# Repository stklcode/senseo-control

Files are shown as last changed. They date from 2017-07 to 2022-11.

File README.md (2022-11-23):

View this project on [CADLAB.io](https://cadlab.io/node/863). 

# Senseo Control 2.0 

A completely rebuilt AVR based hard- and software for Senseo® HD782x coffee machine.
It allows custom setting of cup size and temperature and includes simple support for a second cup size (e.g. espresso) by pushing the buttons longer (2s).

The original project was documented in [this blog post](https://www.stklblog.de/blog/senseo-control-20) (German), including photos of the prototype.

## Functionality

The OEM functionality (coffee, rinsing, auto-off) has been reimplemented (indications adapted to RGB LED) with a few features on top. 

### Features

| |  Input | Action |
|:---:|:---:|:---:|
| ⬤ ⭗ ⬤ | push both coffee buttons | rinsing cycle (pump cold water, until tank is empty) |
| ⬤ ⭗ ⭕ | push single coffee button | 1/2 cups of coffee |
| ⬤ ⭗ ⭕ | push single coffee button for 2s | 1/2 cups of espresso (shorter time, 2s pre-brewing)  |
| ⭕ ⬤ ⭕ | push power button | start / shutdown at any time |
| ⭕ ⭗ ⭕ | 3 minutes idle | Auto-Off |

#### Optional Features

* **Coffee wish** - if enabled (see below), the machine will memorize your coffee wish during heat-up and automatically 
start the coffee when finished, indicating through a violet LED (instead of green) 

### LED Signals

| Color  | Light | Flashing |
|:---:|:---:|:---:|
| red | - | <span style="color:red">◍</span> heating up |
| green  | <span style="color:green">⬤</span> ready  | <span style="color:green">◍</span> coffee running |
| orange | - | <span style="color:orange">◍</span> espresso running |
| blue | <span style="color:blue">⬤</span> rinsing | <span style="color:blue">◍</span> water empty |
| violet | - | <span style="color:violet">◍</span> heating up (coffee wish) |

## Platform

### Hardware

The hardware is based on an **ATtiny26** microcontroller with internal 8MHz RC oscillator.

Power supply is provided by a small transforer with a _78L05_ linear regulator. 
Pump and boiler are controlled by Triacs with isolated MOC30xx drivers.
The original sensors (NTC for temperature, Hall for water tank switch) are directly attached to the new board.

### Schematic and Layout

The prototype has been built in THT on a perfboard, hence the layout provided is compatible to 2.54mm (100mil) grid.
Might as well be used for a PCB. The board is designed to fit the HD7822 model.

Files provided under _hardware/_ are compatible with CadSoft/Autodesk EAGLE™ 6 and above.

### Firmware

The firmware is written in _C_ and comes with a _Makefile_ for use with _avr-gcc_ and _avrdude_.
There are configurations available for _STK500_, _AVR ISP mkII_ and _Pony-STK200_ which can be adapted to your setup.

## Customization

The code is designed to customize functions, timing, temperature and hardware pinning.
To to so, set the corresponding fields in the _main.h_ file:

| Flag | Default | Description |
|---|---|---|
| `TIME_1_ESPRESSO` | 15 | pump time 1 espresso (seconds) |
| `TIME_2_ESPRESSO` | 28 | pump time 2 espressos (seconds) |
| `TIME_1_COFFEE` | 26 | pump time 1 coffee (seconds) |
| `TIME_2_COFFEE` | 52 | pump time 2 coffees (seconds) |
| `OPERATING_TEMPERATURE` | 125 | water temperature (ADC value) |
| `AUTO_OFF_THRESHOLD` | 180 | Auto-Off time (seconds  after last action) |
| `COFFEE_WISH` | 0 | save coffee wish on heat-up (`1` to enable)  |

Pinout, button-thresholds and LED-configuration is also present in this file (should be self-explaining).

## Build Instructions
* Required tools: _avr-gcc_, _avr-objcopy_, _avrdude_ (for flashing only), _make_
* All sources are bundled in the `firmware` directory
* Check `Makefile.config` for the correct settings, especially tool and port for automated flashing.
* On first build you might want to set the correct fuse bits, so run `make fuses`
* Run `make compile info program` for compilation, details about binary, and flashing
* Check `make help` for all available commands

## Notes

The Triacs need heatsink.
The prototype uses approx. 75 x 30 x 1.5 mm (3 x 1.2 x 0.06 in) aluminum sheet, which is about the minimum recommended with a maximum temperature around 70°C (158°F).

<span style="background-color:lightyellow;padding:.5em;border-left:4px orange solid;display:block">**⚡ Danger - High Voltage ⚡**<br>
Working on a live coffee machine involves voltages of 120/230V AC **!** This voltage is applied to the heatsinks and causes hazard on contact.<br>
Please make sure you know what you are doing or consult an authorized professional.<br>
<br>
Cut the power before working on the device.
First tests can be done without main power (supply the µC with 5V from the programmer), Triacs can be tested with low voltage (e.g. 12V~).
On final test use an isolating transformer or at least a RCD.</span>

## License

The project is licensed under [GPL v3](https://www.gnu.org/licenses/gpl-3.0.de.html) license.

## Disclaimer

_"SENSEO"_ is a Trademark of _Koninklijke Philips N.V._ when used for coffee makers and a Trademark of _Sara Lee/De N.V._ when used for coffee pods.
No claim is made to the exclusive right to use _Senseo_ apart from the mark as shown.

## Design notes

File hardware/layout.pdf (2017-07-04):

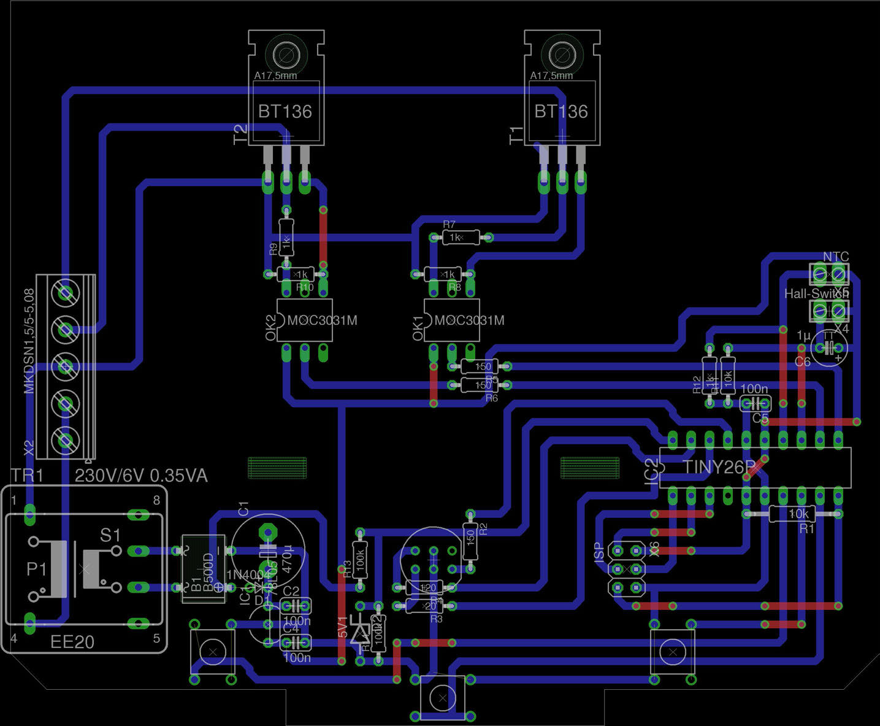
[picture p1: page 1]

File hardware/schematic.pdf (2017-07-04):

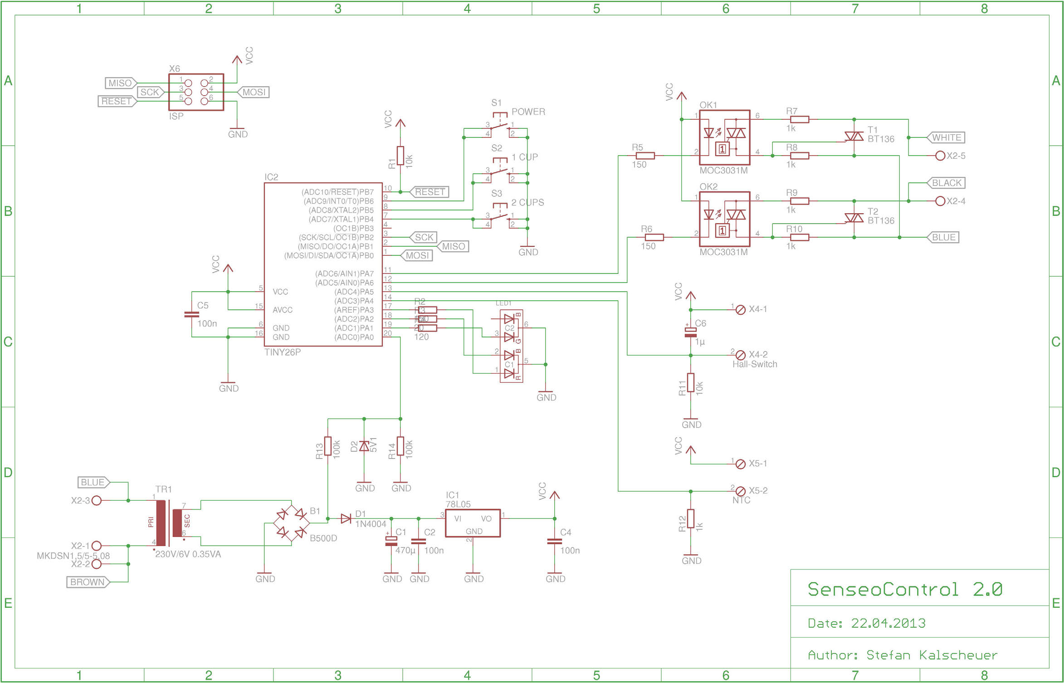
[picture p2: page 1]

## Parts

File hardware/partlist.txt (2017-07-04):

Partlist

Exported from SenseoControl 2.0

Part     Value           Device            Package         Library         Sheet

B1       B500D           B-DIL             B-DIL           rectifier       1
C1       470µ            CPOL-EUE2.5-6     E2,5-6          resistor        1
C2       100n            C-EU025-024X044   C025-024X044    resistor        1
C4       100n            C-EU025-024X044   C025-024X044    resistor        1
C5       100n            C-EU025-024X044   C025-024X044    resistor        1
C6       1µ              CPOL-EUTT2D5      TT2D5           resistor        1
D1       1N4004          DIODE-D-2.5       D-2.5           diode           1
D2       5V1             ZENER-DIODEZD-7.5 ZDIO-7.5        diode           1
IC1      78L05           78L2              TO92-A          linear          1
IC2      TINY26P         TINY26P           DIL20           atmel           1
LED1     LF5             LF5               LF5             led-rgb         1
OK1      MOC3031M        MOC3031M          DIL06           optocoupler     1
OK2      MOC3031M        MOC3031M          DIL06           optocoupler     1
R1       10k             R-EU_0207/12      0207/12         resistor        1
R2       150             R-EU_0204/7       0204/7          resistor        1
R3       20              R-EU_0204/7       0204/7          resistor        1
R4       120             R-EU_0204/7       0204/7          resistor        1
R5       150             R-EU_0204/7       0204/7          resistor        1
R6       150             R-EU_0204/7       0204/7          resistor        1
R7       1k              R-EU_0204/7       0204/7          resistor        1
R8       1k              R-EU_0204/7       0204/7          resistor        1
R9       1k              R-EU_0204/7       0204/7          resistor        1
R10      1k              R-EU_0204/7       0204/7          resistor        1
R11      10k             R-EU_0204/7       0204/7          resistor        1
R12      1k              R-EU_0204/7       0204/7          resistor        1
R13      100k            R-EU_0204/7       0204/7          resistor        1
R14      100k            R-EU_0204/7       0204/7          resistor        1
S1       POWER           10-XXA            B3F-10XX-A      switch-omron    1
S2       1 CUP           10-XXA            B3F-10XX-A      switch-omron    1
S3       2 CUPS          10-XXA            B3F-10XX-A      switch-omron    1
T1       BT136           BT136             TO220AB         triac           1
T2       BT136           BT136             TO220AB         triac           1
TR1      230V/6V 0.35VA  EE20-1            EE20-1          trafo           1
X2       MKDSN1,5/5-5,08 MKDSN1,5/5-5,08   MKDSN1,5/5-5,08 con-phoenix-508 1
X4       Hall-Switch     MPT2              2POL254         con-phoenix-254 1
X5       NTC             MPT2              2POL254         con-phoenix-254 1
X6       ISP             PINHD-2X3         2X03            pinhead         1

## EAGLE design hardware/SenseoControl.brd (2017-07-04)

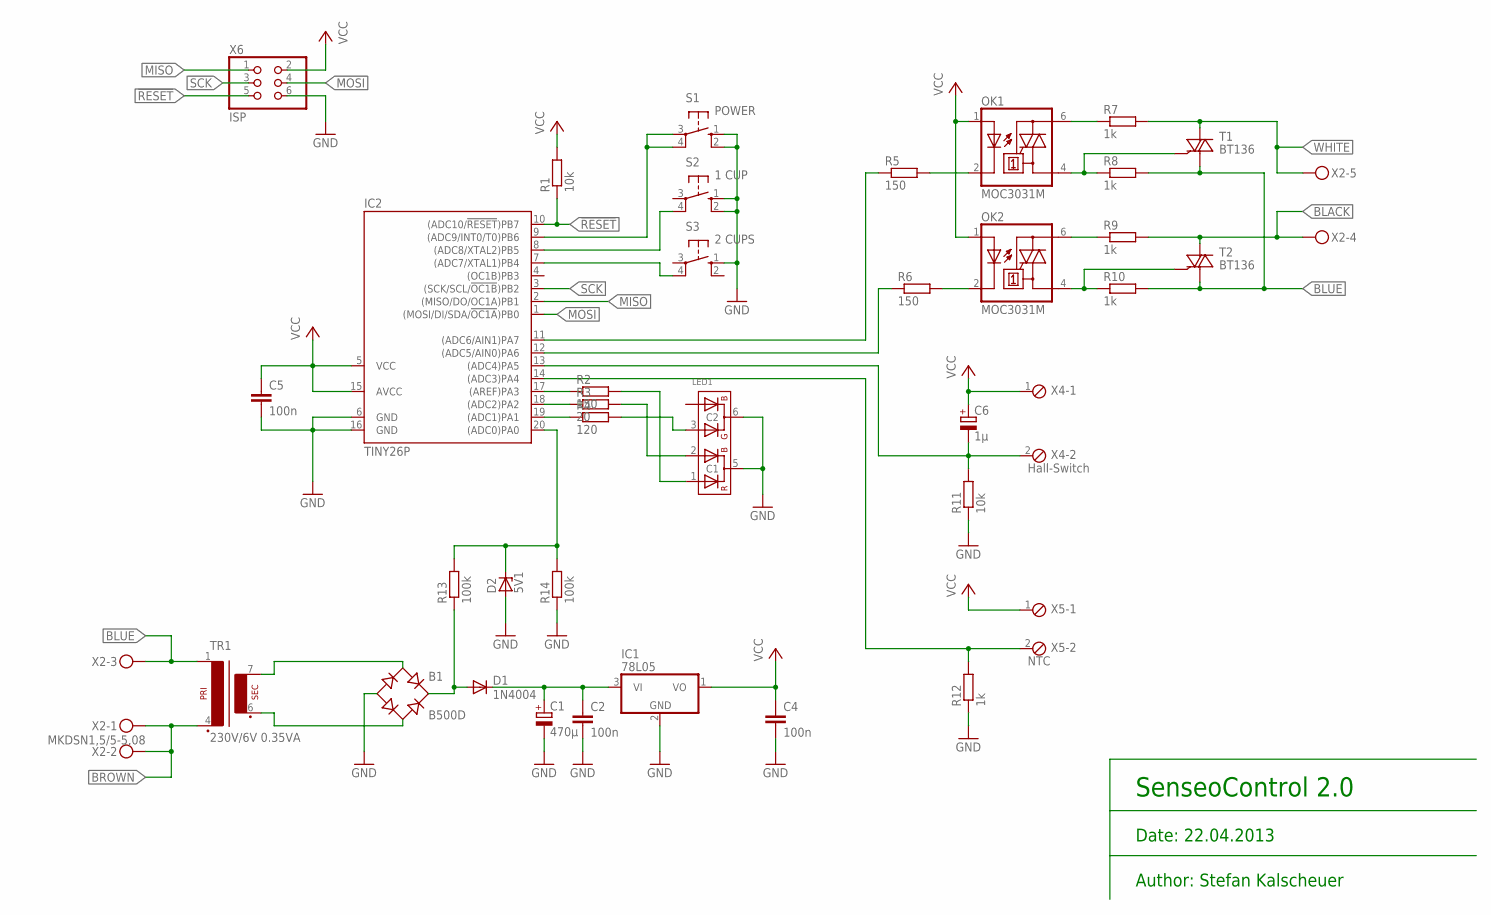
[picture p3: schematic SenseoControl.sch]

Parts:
B1: B500D; B-DIL
C1: 470µ; E2,5-6
C2, C4, C5: 100n; C025-024X044
C6: 1µ; TT2D5
D1: 1N4004; D-2.5
D2: 5V1; ZDIO-7.5
IC1: 78L05; TO92-A
IC2: TINY26P; DIL20
LED1: LF5
OK1, OK2: MOC3031M; DIL06
R1: 10k; 0207/12
R2, R5, R6: 150; 0204/7
R3: 20; 0204/7
R4: 120; 0204/7
R7, R8, R9, R10, R12: 1k; 0204/7
R11: 10k; 0204/7
R13, R14: 100k; 0204/7
S1: POWER; B3F-10XX-A
S2: 1 CUP; B3F-10XX-A
S3: 2 CUPS; B3F-10XX-A
T1, T2: BT136; TO220AB
TR1: 230V/6V 0.35VA; EE20-1
X2: MKDSN1,5/5-5,08
X4: Hall-Switch; 2POL254
X5: NTC; 2POL254
X6: ISP; 2X03

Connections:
!RESET: IC2.10 ((ADC10/!RESET!)PB7), R1.1, X6.5
BLACK: R9.2, T2.2 (A2), X2.4
BLUE: R8.2, R10.2, T1.1 (A1), T2.1 (A1), TR1.1, X2.3
BROWN: TR1.4 (P2), X2.1, X2.2
GND: B1.-, C1.-, C2.2, C4.2, C5.2, D2.A, IC1.2 (GND), IC2.6 (GND), IC2.16 (GND), LED1.5 (C1), LED1.6 (C2), R11.1, R12.1, R14.1, S1.1 (S), S1.2 (S1), S2.1 (S), S2.2 (S1), S3.1 (S), X6.6
MISO: IC2.2 ((MISO/DO/OC1A)PB1), X6.1
MOSI: IC2.1 ((MOSI/DI/SDA/!OC1A!)PB0), X6.4
unnamed: LED1.2 (A-BLUE), R3.2
unnamed: B1.AC1, TR1.7 (S4)
unnamed: OK1.4 (A1), R8.1, T1.3 (G)
unnamed: B1.AC2, TR1.6 (S3)
unnamed: IC2.18 ((ADC2)PA2), R3.1
unnamed: D2.C, IC2.20 ((ADC0)PA0), R13.2, R14.2
unnamed: C1.+, C2.1, D1.C, IC1.3 (VI)
unnamed: IC2.7 ((ADC7/XTAL1)PB4), S3.4 (P1)
unnamed: IC2.8 ((ADC8/XTAL2)PB5), S2.4 (P1)
unnamed: IC2.9 ((ADC9/INT0/T0)PB6), S1.3, S1.4 (P1)
unnamed: IC2.17 ((AREF)PA3), R2.1
unnamed: LED1.3 (A_GREEN), R4.2
unnamed: LED1.1 (A-RED), R2.2
unnamed: B1.+, D1.A, R13.1
unnamed: IC2.19 ((ADC1)PA1), R4.1
unnamed: IC2.11 ((ADC6/AIN1)PA7), R5.1
unnamed: IC2.12 ((ADC5/AIN0)PA6), R6.1
unnamed: OK1.6 (A2), R7.1
unnamed: OK2.6 (A2), R9.1
unnamed: OK2.4 (A1), R10.1, T2.3 (G)
unnamed: OK2.2 (C), R6.2
unnamed: OK1.2 (C), R5.2
unnamed: C6.-, IC2.13 ((ADC4)PA5), R11.2, X4.2
unnamed: IC2.14 ((ADC3)PA4), R12.2, X5.2
SCK: IC2.3 ((SCK/SCL/!OC1B!)PB2), X6.3
VCC: C4.1, C5.1, C6.+, IC1.1 (VO), IC2.5 (VCC), IC2.15 (AVCC), OK1.1 (A), OK2.1 (A), R1.2, X4.1, X5.1, X6.2
WHITE: R7.2, T1.2 (A2), X2.5

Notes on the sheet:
SenseoControl 2.0
Author: Stefan Kalscheuer
Date: 22.04.2013

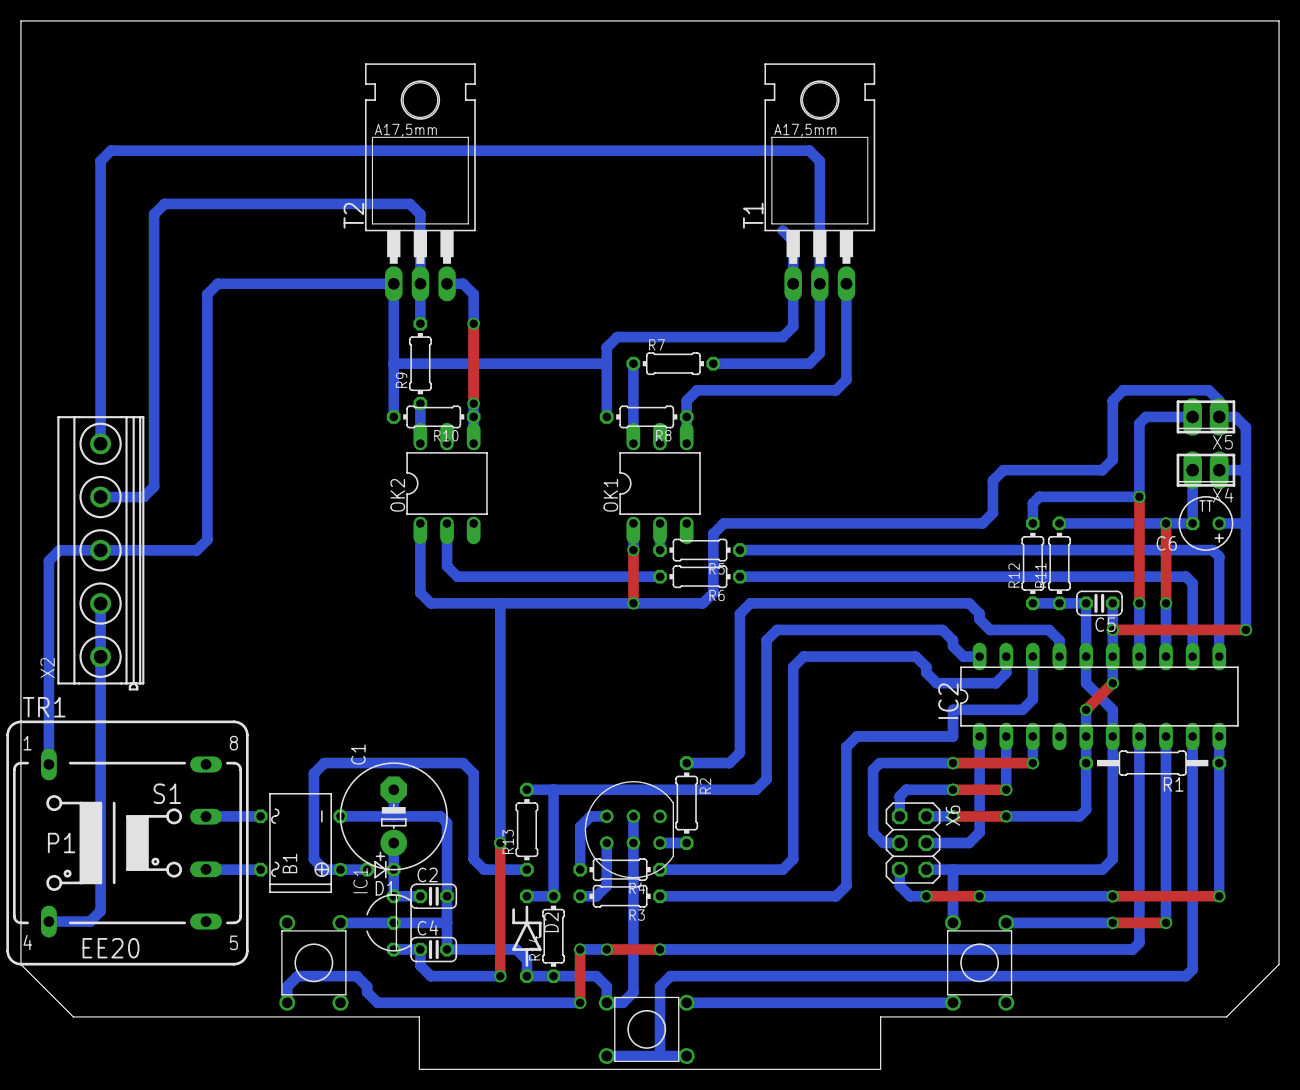
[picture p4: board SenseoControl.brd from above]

Board: 2 copper layers, 120.0 x 100.0 mm, 37 parts (0 on the bottom side), 34 nets.

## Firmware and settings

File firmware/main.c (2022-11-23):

/*****************************************************************************
 *  SenseoControl 2.0                                                        *
 *  Copyright (C) 2013-2022  Stefan Kalscheuer                               *
 *                                                                           *
 *  This program is free software: you can redistribute it and/or modify     *
 *  it under the terms of the GNU General Public License as published by     *
 *  the Free Software Foundation version 3.                                  *
 *                                                                           *
 *  This program is distributed in the hope that it will be useful,          *
 *  but WITHOUT ANY WARRANTY; without even the implied warranty of           *
 *  MERCHANTABILITY or FITNESS FOR A PARTICULAR PURPOSE.  See the            *
 *  GNU General Public License for more details.                             *
 *                                                                           *
 *   You should have received a copy of the GNU General Public License       *
 *   along with this program.  If not, see <https://www.gnu.org/licenses/>.  *
 *****************************************************************************/

/**
 * SenseoControl 2.0
 *
 * @file   main.c
 * @author Stefan Kalscheuer
 * @date   2013-04-22
 * @brief  Main program
 *
 * Platform:  ATtiny26
 *            Internal RC-oscillator 8 MHz, CKDIV8 Enabled
 */

#define F_CPU    1000000UL

// includes
#include <util/delay.h>
#include <avr/interrupt.h>
#include <avr/io.h>
#include "main.h"

// variables:
volatile unsigned int time_counter;                 // Global time counter (ms).
volatile unsigned int user_time_counter = 0;        // Universal time counter (ms).
volatile unsigned int sec_counter = 0;              // Second-counter (for AutoOff).
volatile unsigned int button_1_cup_counter = 0;     // Left button counter (1 cup).
volatile unsigned int button_2_cup_counter = 0;     // Left button counter (2 cups).
volatile unsigned char button_power_counter = 0;    // Power button counter.
volatile unsigned char led = 0;                     // LED status flags.
volatile unsigned char state;                       // Water-, temperature-, clean-flags.
volatile unsigned char make_coffee = NO_COFFEE;     // Coffee mode flag.
volatile unsigned char pump_time = 0;               // Pump time.

/**
 * Main program.
 *
 * @return This method should never terminate.
 */
int main(void) {
    init();                                                 // Initialization.
    power_off();                                            // Power off after init sequence.

    while (1) {                                             // Main loop.
        if (sec_counter >= AUTO_OFF_THRESHOLD) {
            button_power_counter = BUTTON_THRESHOLD;        // Check for AutoOff Timer (generate OnOff-button push).
        }

        update_water();                                     // Update water state.
        update_temperature();                               // Update temperature.

        if (button_power_counter >= BUTTON_THRESHOLD) {     // Button "OnOff" pushed:
            set_bit(TRIAC_BOILER_w, TRIAC_BOILER_pin);      // Boiler off
            make_coffee = NO_COFFEE;                        // Clear coffee flag.

            while (button_power_counter > 0);               // Wait until button is released (debounce)

            power_off();                                    // Call power off sequence

            button_power_counter = BUTTON_THRESHOLD;        // Debounce again after wake up
            while (button_power_counter > 0);
        }

        process_buttons();

        if (state & S_WATER) {                                  // Water OK:
            if (state & S_CLEAN) {                              // If clean-flag is set:
                do_clean();
            } else if (state & S_TEMP) {                        // Temperature OK:
                set_bit(TRIAC_BOILER_w, TRIAC_BOILER_pin);      // Boiler off.
                led = GREEN;                                    // Set green LED.
                if (make_coffee > NO_COFFEE) {                  // If coffee flag is set:
                    do_coffee();
                }
            } else {                                            // Temperature too low.
                clear_bit(TRIAC_BOILER_w, TRIAC_BOILER_pin);    // Boiler on.
                if (make_coffee > NO_COFFEE) {                  // Set violet LED blink if coffee wish is saved.
                    led = VIOLET_BLINK;
                } else {                                        // Set red LED blink if no coffee wish is saved.
                    led = RED_BLINK;
                }
            }
        } else {                                                // Water too low:
            set_bit(TRIAC_BOILER_w, TRIAC_BOILER_pin);          // Boiler off.
            set_bit(TRIAC_PUMP_w, TRIAC_PUMP_pin);              // Pump off.
            led = BLUE_BLINK;                                   // Set blue LED blink.
        }
    }
}

/**
 * Initializes relevant bits, timer and ADC.
 */
void init() {
    clear_bit(ZERO_CROSSING_ddr, ZERO_CROSSING_pin);    // Zero crossing detection pins as input.
    clear_bit(ZERO_CROSSING_w, ZERO_CROSSING_pin);      // No internal pull-up (for ADC).

    clear_bit(BUTTON_1_CUP_ddr, BUTTON_1_CUP_pin);      // Button pins as input.
    set_bit(BUTTON_1_CUP_w, BUTTON_1_CUP_pin);          // Activate internal pull-ups.
    clear_bit(BUTTON_2_CUP_ddr, BUTTON_2_CUP_pin);
    set_bit(BUTTON_2_CUP_w, BUTTON_2_CUP_pin);
    clear_bit(BUTTON_POWER_ddr, BUTTON_POWER_pin);
    set_bit(BUTTON_POWER_w, BUTTON_POWER_pin);

    set_bit(LED_RED_ddr, LED_RED_pin);                  // LED pins as output.
    clear_bit(LED_RED_w, LED_RED_pin);                  // Clear outputs (LEDs off).
    set_bit(LED_GREEN_ddr, LED_GREEN_pin);
    clear_bit(LED_GREEN_w, LED_GREEN_pin);
    set_bit(LED_BLUE_ddr, LED_BLUE_pin);
    clear_bit(LED_BLUE_w, LED_BLUE_pin);

    clear_bit(SENSOR_MAGNET_ddr, SENSOR_MAGNET_pin);    // Sensor pins as input.
    clear_bit(SENSOR_MAGNET_w, SENSOR_MAGNET_pin);      // No internal pull-up (for ADC).
    clear_bit(SENSOR_TEMP_ddr, SENSOR_TEMP_pin);
    clear_bit(SENSOR_TEMP_w, SENSOR_TEMP_pin);

    set_bit(TRIAC_BOILER_ddr, TRIAC_BOILER_pin);        // Triac pins as output.
    set_bit(TRIAC_BOILER_w, TRIAC_BOILER_pin);          // Set outputs high (triac off).
    set_bit(TRIAC_PUMP_ddr, TRIAC_PUMP_pin);
    set_bit(TRIAC_PUMP_w, TRIAC_PUMP_pin);

    ADCSR = (1 << ADEN) | (1 << ADPS1);                 // Enable ADC, prescaler division factor 4.

    // TIMER1
    set_bit(TCCR1B, CTC1);                              // Set timer 1 to CTC-Mode.
    clear_bit(TCCR1B, CS11);                            // Prescaler 8.
    set_bit(TCCR1B, CS12);
    clear_bit(TCCR1B, CS11);
    clear_bit(TCCR1B, CS10);
    OCR1C = 124;                                        // Period of 1 ms.

    cli();                                              // Disable interrupts.
    clear_bit(GIMSK, INT0);                             // Disable interrupt 0.
    set_bit(TIMSK, TOIE1);                              // Activate timer 1.
    sei();                                              // Enable interrupts.
}

/**
 * Clear bits and set controller to sleep mode.
 */
void power_off(void) {
    cli();                                  // Disable interrupts.
    set_bit(GIMSK, INT0);                   // Activate interrupt 0 (for wake-up).
    clear_bit(TIMSK, TOIE1);                // Deactivate timer 1.
    sei();                                  // Re-enable interrupts.

    clear_bit(LED_RED_w, LED_RED_pin);      // Clear LED outputs.
    clear_bit(LED_GREEN_w, LED_GREEN_pin);
    clear_bit(LED_BLUE_w, LED_BLUE_pin);

    set_bit(MCUCR, SM1);                    // Activate power-down mode.
    clear_bit(MCUCR, SM0);
    set_bit(MCUCR, SE);
    asm volatile("sleep"::);

    // Entrance point after wake-up.
    time_counter = 0;                       // Reset counter.
    sec_counter = 0;
    cli();                                  // Disable interrupts.
    clear_bit(GIMSK, INT0);                 // Disable interrupt 0.
    set_bit(TIMSK, TOIE1);                  // Enable timer 1.
    sei();                                  // Re-enable interrupts.
}

/**
 * Checks hall sensor for water level.
 */
void update_water(void) {
    ADMUX = SENSOR_MAGNET_adc | (1 << ADLAR);
    set_bit(ADCSR, ADSC);
    loop_until_bit_is_clear(ADCSR, ADSC);
    unsigned char sense = ADCH;
    if (((state & S_WATER) && sense > WATER_LOW) || (!(state & S_WATER) && sense >= WATER_OK)) {
        set_bit(state, S_WATER);
    } else {
        clear_bit(state, S_WATER);
    }
}

/**
 * Checks NTC sensor for temperature state.
 */
void update_temperature(void) {
    ADMUX = SENSOR_TEMP_adc | (1 << ADLAR);
    set_bit(ADCSR, ADSC);
    loop_until_bit_is_clear(ADCSR, ADSC);
    unsigned char sense = ADCH;
    if (sense >= OPERATING_TEMPERATURE) {
        set_bit(state, S_TEMP);
    } else {
        clear_bit(state, S_TEMP);
    }
}

/**
 * Checks for zero crossing (with fixed offset)
 *
 * @return Raw ADC value.
 */
unsigned int detect_zero_crossing() {
    ADMUX = ZERO_CROSSING_adc;
    set_bit(ADCSR, ADSC);
    loop_until_bit_is_clear(ADCSR, ADSC);
    unsigned char sense_L = ADCL;
    unsigned char sense_H = ADCH;
    return (sense_H << 8) | sense_L;
}

/**
 * Process button inputs and update states accordingly.
 */
static void process_buttons(void) {
    if (button_1_cup_counter >= BUTTON_CLEAN_THR && button_2_cup_counter >= BUTTON_CLEAN_THR) {
        // Both coffee buttons pushed: enter clean mode.
        set_bit(state, S_CLEAN);    // Set clean flag.
        led = BLUE;                 // Set blue LED.
        while (button_1_cup_counter > 0 && button_2_cup_counter > 0);   // Debounce buttons.
    } else if (button_1_cup_counter >= BUTTON_THRESHOLD && button_2_cup_counter < BUTTON_THRESHOLD) {
        // Left coffee button pushed: call espresso.
        sec_counter = 0;    // Reset AutoOff counter.

        if ((state & S_WATER) && (state & S_TEMP)) {            // Machine ready:
            while (button_1_cup_counter > 0) {                  // Check if button is pushed long time.
                if (button_1_cup_counter > BUTTON_LONG_THR) {   // Button pushed for a long time:
                    make_coffee = ONE_ESPRESSO;                   // Set coffee flag to 1 (1 espresso).
                    button_1_cup_counter = 0;                   // Clear button counter.
                }
            }
            if (make_coffee != ONE_ESPRESSO) {
                make_coffee = ONE_COFFEE;                       // Set coffee flag to 3 (1 coffee) otherwise.
            }
        } else if (COFFEE_WISH) {                               // Save coffee wish.
            make_coffee = ONE_COFFEE;
        }
    } else if (button_1_cup_counter < BUTTON_THRESHOLD && button_2_cup_counter >= BUTTON_THRESHOLD) {
        // Right coffee button pushed: call coffee.
        sec_counter = 0;                                        // Reset AutoOff counter.

        if ((state & S_WATER) && (state & S_TEMP)) {            // Machine ready:
            while (button_2_cup_counter > 0) {                  // Check if button is pushed long time.
                if (button_2_cup_counter > BUTTON_LONG_THR) {   // Button pushed for a long time:
                    make_coffee = TWO_ESPRESSO;                 // Set coffee flag to 2 (2 espresso).
                    button_2_cup_counter = 0;                   // Clear button counter.
                }
            }
            if (make_coffee != TWO_ESPRESSO) {
                make_coffee = TWO_COFFEE;                       // Set coffee flag to 4 (2 coffee) otherwise.
            }
        } else if (COFFEE_WISH) {                               // Save coffee wish
            make_coffee = TWO_COFFEE;
        }
    }
}

/**
 * Execute cleaning routine.
 * Pump water without additional heating, until the water tank is empty or the power button is pushed.
 */
static void do_clean(void) {
    set_bit(TRIAC_BOILER_w, TRIAC_BOILER_pin);          // Boiler off.
    clear_bit(state, S_ESC);                            // Init escape-flag.

    // Pump until water is empty or escape flag is set.
    while ((state & S_WATER) && (state & S_ESC)) {
        // Detect zero crossing and trigger impulse for the pump triac.
        if (detect_zero_crossing() <= 100) {
            clear_bit(TRIAC_PUMP_w, TRIAC_PUMP_pin);
            _delay_ms(3);
            set_bit(TRIAC_PUMP_w, TRIAC_PUMP_pin);
        }

        // Update water state.
        update_water();

        // Check power button counter and set escape flag.
        if (button_power_counter > BUTTON_THRESHOLD) {
            set_bit(state, S_ESC);
        }
    }

    // Clear clean flag.
    clear_bit(state, S_CLEAN);
}

/**
 * Execute the actual coffee making routine.
 */
static void do_coffee(void) {
    // Set orange LED blink for espresso and green blink for coffee.
    if (IS_ESPRESSO(make_coffee)) {
        led = ORANGE_BLINK;
    } else {
        led = GREEN_BLINK;
    }

    // Determine the correct pump time for espresso (including 2s preinfusion break) and coffee.
    switch (make_coffee) {
        case ONE_ESPRESSO:
            pump_time = TIME_1_ESPRESSO;
            break;
        case 2:
            pump_time = TIME_2_ESPRESSO;
            break;
        case ONE_COFFEE:
            pump_time = TIME_1_COFFEE;
            break;
        case TWO_COFFEE:
            pump_time = TIME_2_COFFEE;
            break;
        default:
            make_coffee = NO_COFFEE;
    }

    user_time_counter = 0;      // Reset user time counter.
    clear_bit(state, S_ESC);    // Init escape flag.

    // loop until pump time is reached or water is empty
    while (user_time_counter < (pump_time * 1000) && (state & S_WATER) && !(state & S_ESC)) {
        // Check for preinfusion break.
        if ((IS_COFFEE(make_coffee) || (user_time_counter < 2000 || user_time_counter > 4000)) &&
            detect_zero_crossing() <= 100) {            // Detect zero crossing.
            // Generate trigger impulse for pump triac.
            clear_bit(TRIAC_PUMP_w, TRIAC_PUMP_pin);
            _delay_ms(3);
            set_bit(TRIAC_PUMP_w, TRIAC_PUMP_pin);
        }

        // Update water state.
        update_water();

        // Check for power button counter and set escape flag.
        if (button_power_counter > BUTTON_THRESHOLD) {
            set_bit(state, S_ESC);
        }
    }

    set_bit(TRIAC_PUMP_w, TRIAC_PUMP_pin);  // Pump off
    make_coffee = NO_COFFEE;                // Clear coffee flag.
    sec_counter = 0;                        // Reset AutoOff timer.
}

/**
 * Dummy function for wake-up.
 */
ISR ( INT0_vect) {
    // Nothing to do here.
}

/**
 * Timer interrupt. Increments counters and controls LED.
 */
ISR ( TIMER1_OVF1_vect) {
    if (time_counter < 1000)
        time_counter++;         // Global milliseconds counter and seconds counter (for AutoOff).
    else {
        time_counter = 0;
        sec_counter++;
    }
    user_time_counter++;        // Universal counter (for pump time).

    unsigned char leds_blink_on;         // Status flag for blinking LEDs with 1Hz.
    if (time_counter < 499) {
        leds_blink_on = 1;
    } else {
        leds_blink_on = 0;
    }

    if (led & (1 << LED_RED_ON) || (led & (1 << LED_RED_BLINK) && leds_blink_on)) {
        set_bit(LED_RED_w, LED_RED_pin);
    } else {
        clear_bit(LED_RED_w, LED_RED_pin);
    }
    if (led & (1 << LED_GREEN_ON) || (led & (1 << LED_GREEN_BLINK) && leds_blink_on)) {
        set_bit(LED_GREEN_w, LED_GREEN_pin);
    } else {
        clear_bit(LED_GREEN_w, LED_GREEN_pin);
    }
    if (led & (1 << LED_BLUE_ON) || (led & (1 << LED_BLUE_BLINK) && leds_blink_on)) {
        set_bit(LED_BLUE_w, LED_BLUE_pin);
    } else {
        clear_bit(LED_BLUE_w, LED_BLUE_pin);
    }

    if (bit_is_clear(BUTTON_1_CUP_r, BUTTON_1_CUP_pin)) {   // Left button counter.
        if (button_1_cup_counter < 65535) {
            button_1_cup_counter++;
        }
    } else {
        if (button_1_cup_counter > 0) {
            button_1_cup_counter--;
        }
    }

    if (bit_is_clear(BUTTON_2_CUP_r, BUTTON_2_CUP_pin)) {   // Right button counter.
        if (button_2_cup_counter < 65535) {
            button_2_cup_counter++;
        }
    } else {
        if (button_2_cup_counter > 0) {
            button_2_cup_counter--;
        }
    }

    if (bit_is_clear(BUTTON_POWER_r, BUTTON_POWER_pin)) {   // Power button counter.
        if (button_power_counter < 255) {
            button_power_counter++;
        }
    } else {
        if (button_power_counter > 0) {
            button_power_counter--;
        }
    }
}

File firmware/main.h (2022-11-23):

/*****************************************************************************
 *  SenseoControl 2.0                                                        *
 *  Copyright (C) 2013-2018  Stefan Kalscheuer                               *
 *                                                                           *
 *  This program is free software: you can redistribute it and/or modify     *
 *  it under the terms of the GNU General Public License as published by     *
 *  the Free Software Foundation version 3.                                  *
 *                                                                           *
 *  This program is distributed in the hope that it will be useful,          *
 *  but WITHOUT ANY WARRANTY; without even the implied warranty of           *
 *  MERCHANTABILITY or FITNESS FOR A PARTICULAR PURPOSE.  See the            *
 *  GNU General Public License for more details.                             *
 *                                                                           *
 *   You should have received a copy of the GNU General Public License       *
 *   along with this program.  If not, see <https://www.gnu.org/licenses/>.  *
 *****************************************************************************/

/**
 * SenseoControl 2.0
 *
 * @file   main.h
 * @author Stefan Kalscheuer
 * @date   2013-04-22
 */

/********************
 * User settings:
 */
#define TIME_1_ESPRESSO       15    // Pump times in seconds.
#define TIME_2_ESPRESSO       28
#define TIME_1_COFFEE         26
#define TIME_2_COFFEE         52
#define OPERATING_TEMPERATURE 125   // ADC threshold for water temperature.
#define COFFEE_WISH           0     // Save coffee wish while heating up.
/*
 ********************/

// Function macros for setting and clearing bits.
#define set_bit(var, bit)   ((var) |= (1 << (bit)))
#define clear_bit(var, bit) ((var) &= (unsigned)~(1 << (bit)))

#define ZERO_CROSSING_w     PORTA   // Zero crossing detection.
#define ZERO_CROSSING_r     PINA
#define ZERO_CROSSING_pin   0
#define ZERO_CROSSING_ddr   DDRA
#define ZERO_CROSSING_adc   0

#define BUTTON_1_CUP_w      PORTB   // Left button.
#define BUTTON_1_CUP_r      PINB
#define BUTTON_1_CUP_pin    4
#define BUTTON_1_CUP_ddr    DDRB

#define BUTTON_2_CUP_w      PORTB   // Right button.
#define BUTTON_2_CUP_r      PINB
#define BUTTON_2_CUP_pin    5
#define BUTTON_2_CUP_ddr    DDRB

#define BUTTON_POWER_w      PORTB   // Power button.
#define BUTTON_POWER_r      PINB
#define BUTTON_POWER_pin    6
#define BUTTON_POWER_ddr    DDRB

#define LED_RED_w           PORTA   // Red LED.
#define LED_RED_r           PINA
#define LED_RED_pin         3
#define LED_RED_ddr         DDRA
#define LED_RED_ON          0
#define LED_RED_BLINK       1

#define LED_GREEN_w         PORTA   // Green LED.
#define LED_GREEN_r         PINA
#define LED_GREEN_pin       1
#define LED_GREEN_ddr       DDRA
#define LED_GREEN_ON        2
#define LED_GREEN_BLINK     3

#define LED_BLUE_w          PORTA   // Blue LED.
#define LED_BLUE_r          PINA
#define LED_BLUE_pin        2
#define LED_BLUE_ddr        DDRA
#define LED_BLUE_ON         4
#define LED_BLUE_BLINK      5

#define SENSOR_MAGNET_w     PORTA   // Hall switch (water).
#define SENSOR_MAGNET_r     PINA
#define SENSOR_MAGNET_pin   5
#define SENSOR_MAGNET_ddr   DDRA
#define SENSOR_MAGNET_adc   4

#define WATER_LOW           30      // ADC threshold for low water.
#define WATER_OK            100     // ADC threshold for water OK.

#define SENSOR_TEMP_w       PORTA   // NTC (temperature)
#define SENSOR_TEMP_r       PINA
#define SENSOR_TEMP_pin     4
#define SENSOR_TEMP_ddr     DDRA
#define SENSOR_TEMP_adc     3

#define TRIAC_BOILER_w      PORTA   // Boiler triac.
#define TRIAC_BOILER_r      PINA
#define TRIAC_BOILER_pin    6
#define TRIAC_BOILER_ddr    DDRA

#define TRIAC_PUMP_w        PORTA   // Pump triac.
#define TRIAC_PUMP_r        PINA
#define TRIAC_PUMP_pin      7
#define TRIAC_PUMP_ddr      DDRA

#define AUTO_OFF_THRESHOLD  180     // AutoOff threshold (seconds).
#define BUTTON_CLEAN_THR    30      // Button threshold for cleaning mode (ms).
#define BUTTON_THRESHOLD    100     // Button threshold (ms).
#define BUTTON_LONG_THR     1500    // Button threshold for long time push (ms).

// Global state flags.
#define S_WATER             0
#define S_TEMP              1
#define S_CLEAN             2
#define S_ESC               3

// Coffee mode flags.
#define NO_COFFEE     0
#define ONE_ESPRESSO  1
#define TWO_ESPRESSO  2
#define ONE_COFFEE    3
#define TWO_COFFEE    4
#define IS_COFFEE(VAR) (VAR > 2)
#define IS_ESPRESSO(VAR) (VAR > 0 && VAR < 3)
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

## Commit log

2017-07-04 Code reformatted
    Constants for pump times in main.h (more readable code, easier to adjust)
2017-07-04 Defined constant flags for LED colors
2017-07-04 Coffee wish implemented with violet led indicator
2017-07-04 Schematic and layout added
    [SenseoControl.brd, SenseoControl.sch]
2017-07-04 ReadMe, Partlist, minor restructuring
    [SenseoControl.brd, SenseoControl.sch]
2022-11-23 Switched to size optimization
2022-11-23 Replaced 5 step if-else by switch-case
    [main.c, main.h]
2022-11-23 extract button processing and coffee/cleaning routines into functions
